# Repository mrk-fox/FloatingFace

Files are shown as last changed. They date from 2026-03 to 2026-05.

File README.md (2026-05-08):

<div align="center">
<h1>FloatingFace</h1><br>
  
A three-string-mounted small multifunctional cable roboter concept. <br>

 



<br>

Flowers
<div align="left">v1.0 aka "Floaty"</div>
</div>
<br>

FloatingFace is a roboter, mounted by 3mm paracord ropes at three points arranged in a triangle which achieves movement withing and under these 3 mounting points by tensioning or loosening each these ropes.

## Key features

- 3-points mount
- cheeseplate with additional servo for mechanization
- automatic calibration
- custom driver PCB with three TMC2209 slots
- redundant visual and magnetic travel distance encoder
- AS5600 magnetic encoders
- MPU5060
- possibility for rope pulley if higher loads applied

I built this project as proof-of-concept system for a 3-point-mounted, portable cable roboter with an universal extensions interface.

## PCB

Floaty has a custom-designed driver developer board for three TMC2209 drivers. Look at the design! <br>
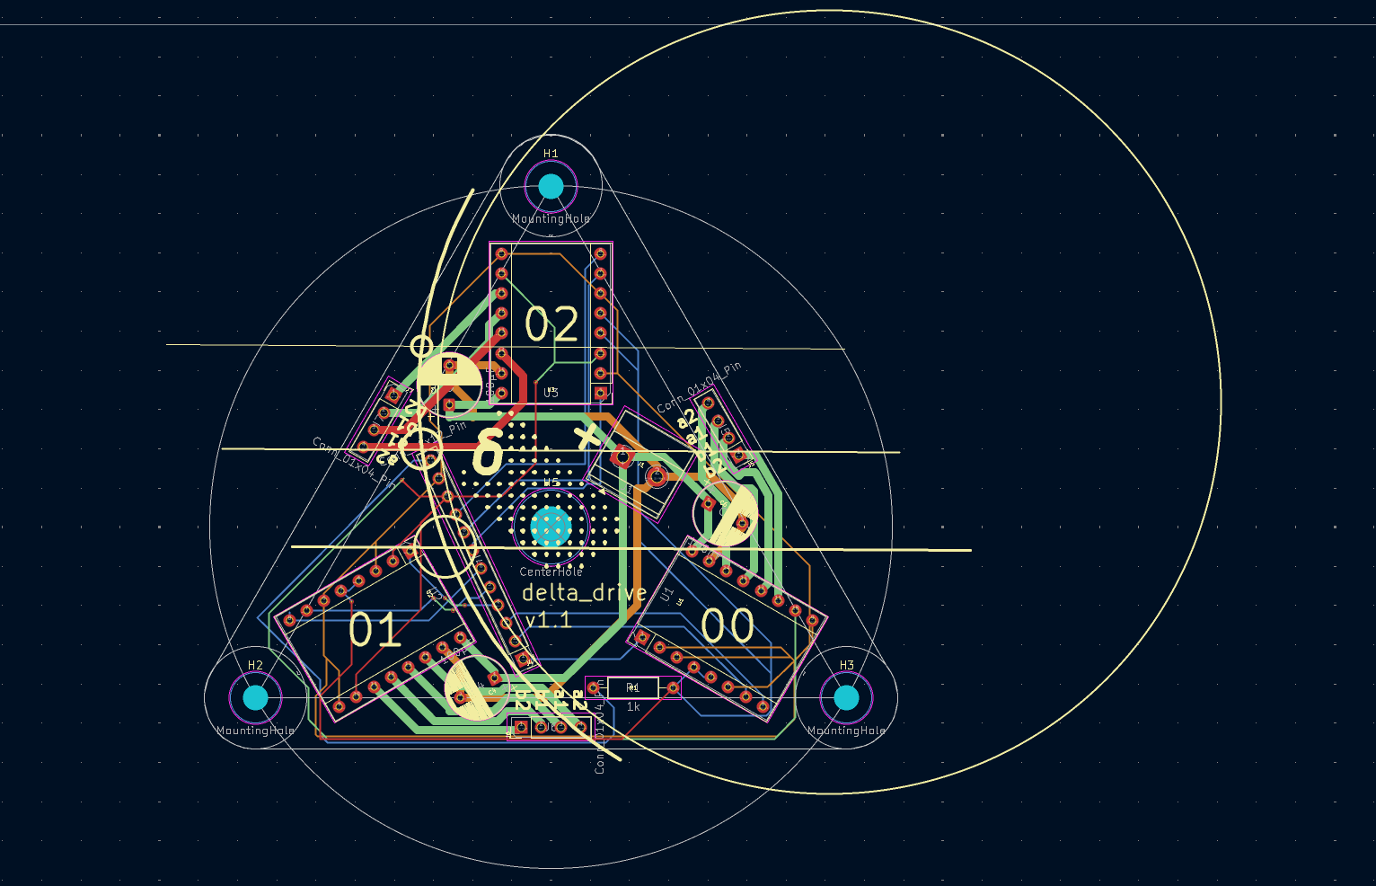
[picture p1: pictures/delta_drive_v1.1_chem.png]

Thats all the layers overlapped...
<br><br><br>
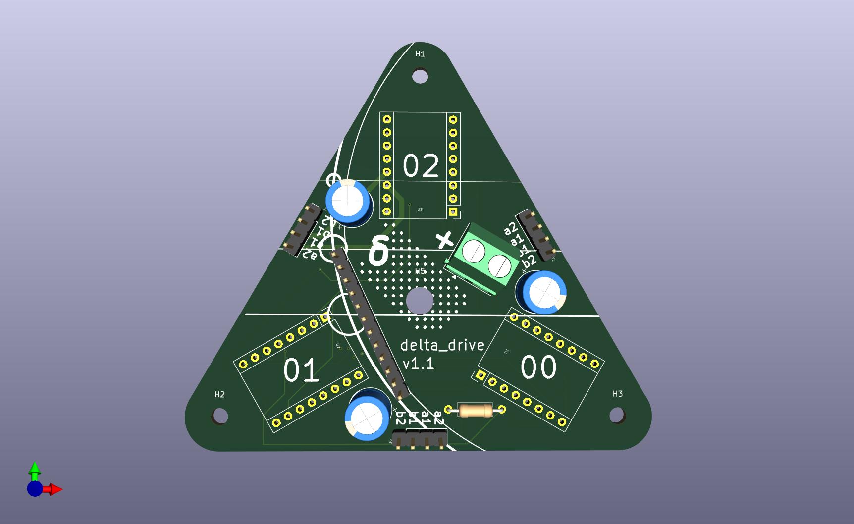
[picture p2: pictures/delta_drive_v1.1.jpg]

...and thats the front design. There is nothing on the back
<br><br><br>
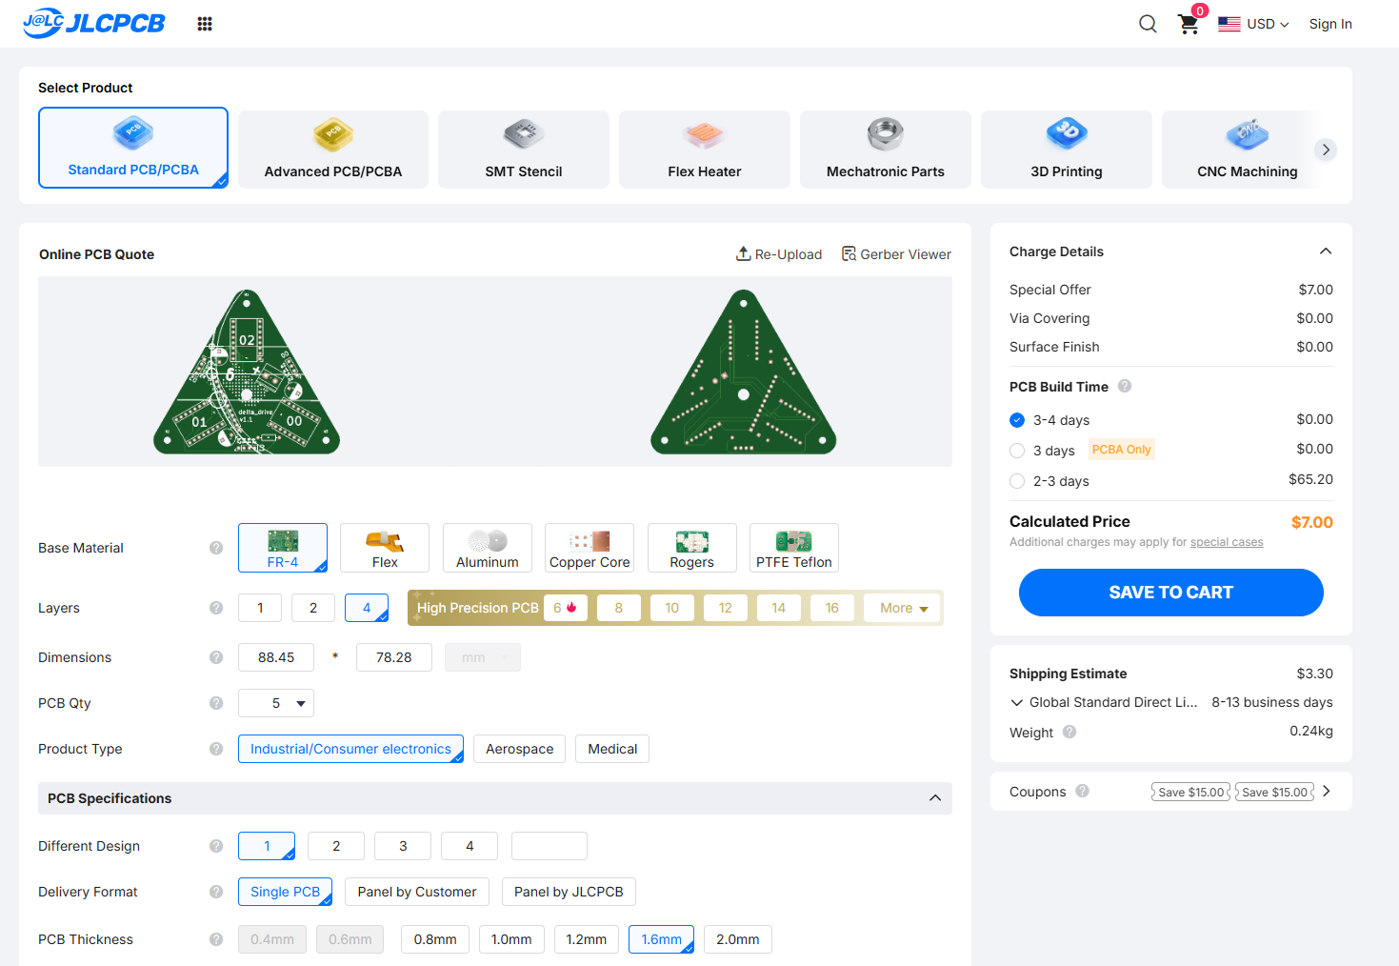
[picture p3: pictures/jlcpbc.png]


## Schematic
<br>
The overview schematic implementing a TCA9548 for the I2C controll of the three AS5600 sensors looks like this:
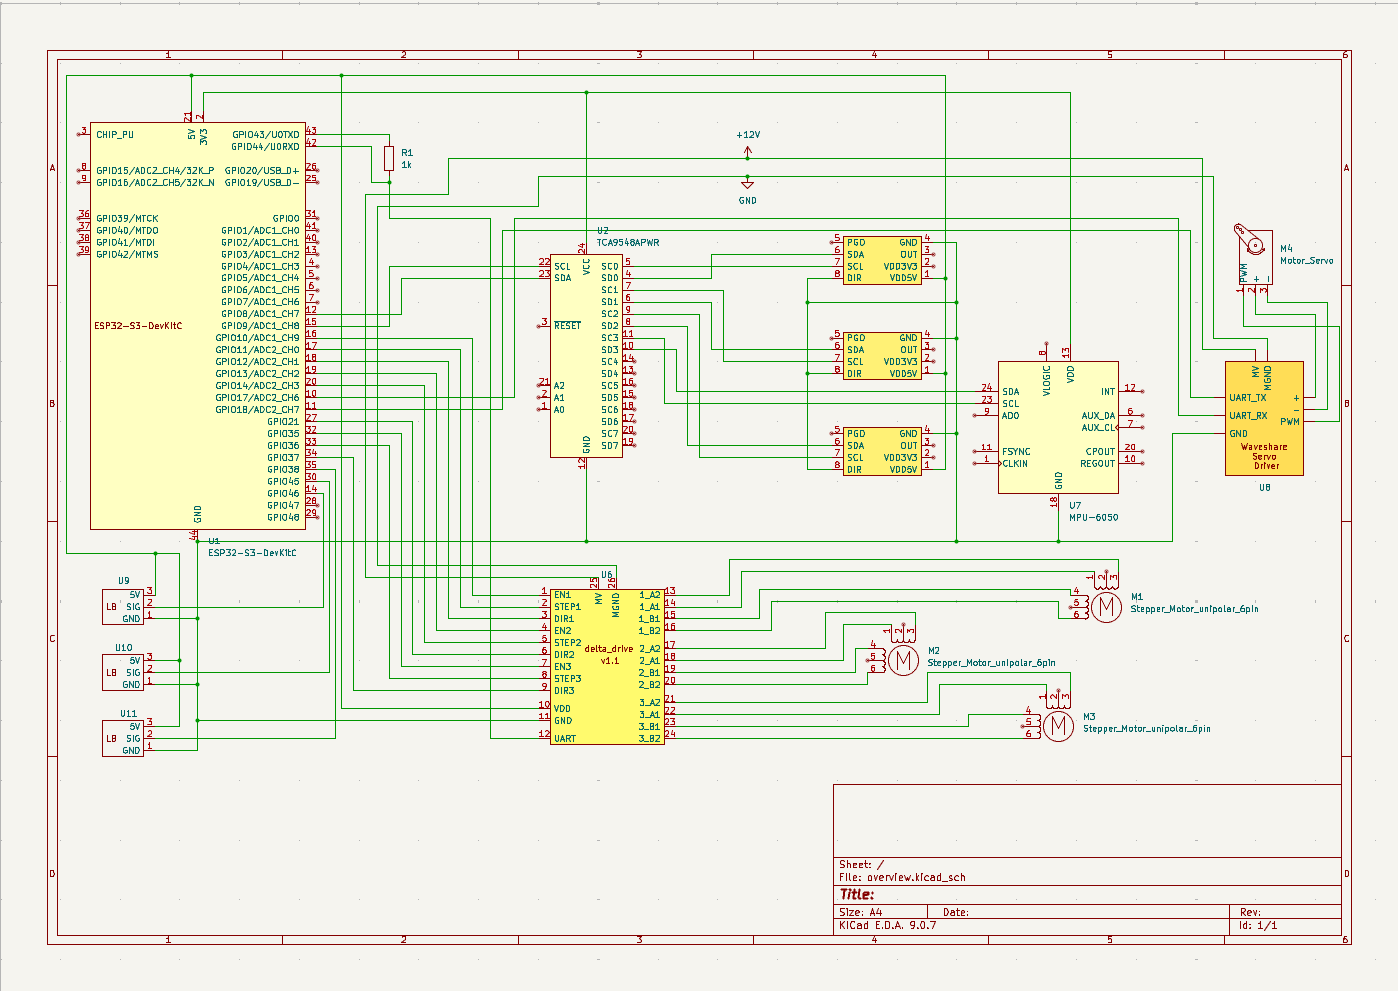
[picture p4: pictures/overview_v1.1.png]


and that is the schematic for the delta_drive v1.1:
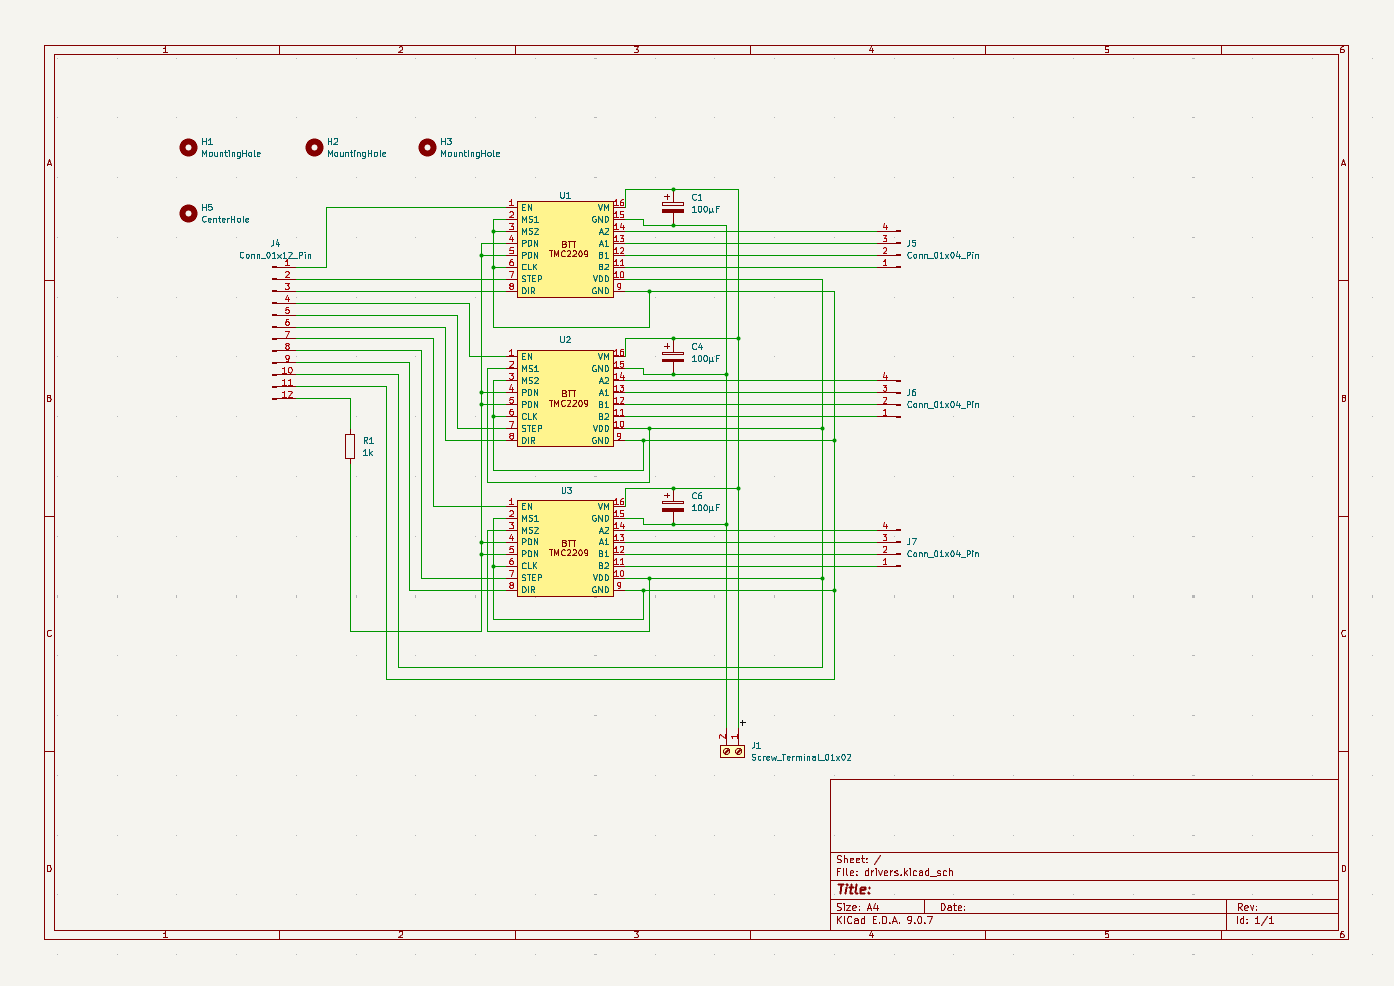
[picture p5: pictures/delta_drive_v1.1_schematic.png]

https://github.com/mrk-fox/FloatingFace/blob/main/pictures/delta_drive_v1.1_schematic.png

## Math
The basics were worked out with simple linear algebra, which are explained in this video together with the calibration process:

[The math behind "Floaty", the cable roboter](https://youtu.be/A8Sq22G1rsY)

Further, to make the implementation easier, all the calculation were modelled in Simulink:
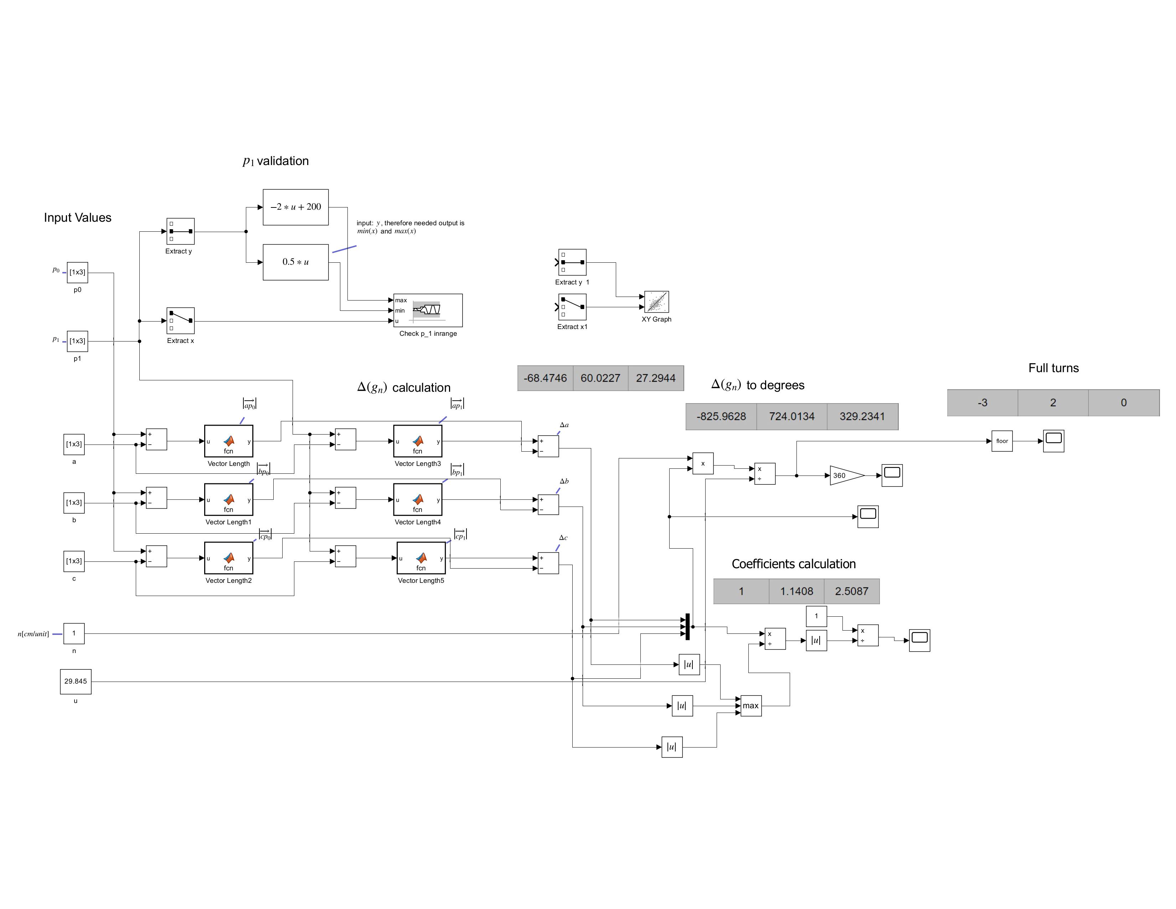
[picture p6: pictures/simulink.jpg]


<br>

The movement algorithm itself works on command through these steps:
1. Validate coordinates
2. Calculate $\Delta(g_n)$ (individual motor run vectors)
3. Calculate time-based movement coefficients $c(\Delta(g_n))$
4. Move in accordance to coefficitens slowly until all motor sensors register rising edge on light sensor
5. Re-calculate path
6. Move fast using PCNT counters
7. Slow down 2 guide sensor revolutions before movement finish
8. Proceed until finish on magnetic encoders feedback
9. Calibrate angles on finish

For angle calibration, Floaty uses the MP5060 sensor which gives an angle relative to gravity and the direction of the orthogonal of the angled face of the sensor. With that data an iterative funciton is started ajusting one motor step at a time until an angle less than 10 degrees is reached. 

## Assembly
The assembly is currently a prediciton of the possible steps. I doubt, that anyone will build this before me, but here we go:

1. Begin with the level one baseplate assemble the motors with the line drums and place them onto the baseplate
2. Mount the Servo and the MCU to the motor mount and baseplate
3. Assemble the 20x20 frame hexagon and mount the baseplate to the hexagon together with the line guides/sensing units
4. Assemble the secon level (electronics) and connect all electronics! (see below)
5. Fix everything together with the threaded rods and the spacers
6. Add the cheeseplate
7. Flash the firmware

## Cables

As the size of the robot is constrainted to certain limits, cable routing is crutial to ensure a safe and reliable operation. The following rules apply:
1. Zip-ties packaging the cable strands shoukd be placed every 2cm (0.787in)
2. Every cable leading to the line measurment units/motos should be placed in the through-leading holes of the appropriate third of the robot
3. A safe-zone of 1cm (0.393in) around the perimeter of the cutout of the basement plate for the line rolls should be cable-free to ensure a tangle-free operation
The mounting is done through running zip ties around the vertical spacers for the levels and the cable holes on the baseplates themselves.

## Zine Page

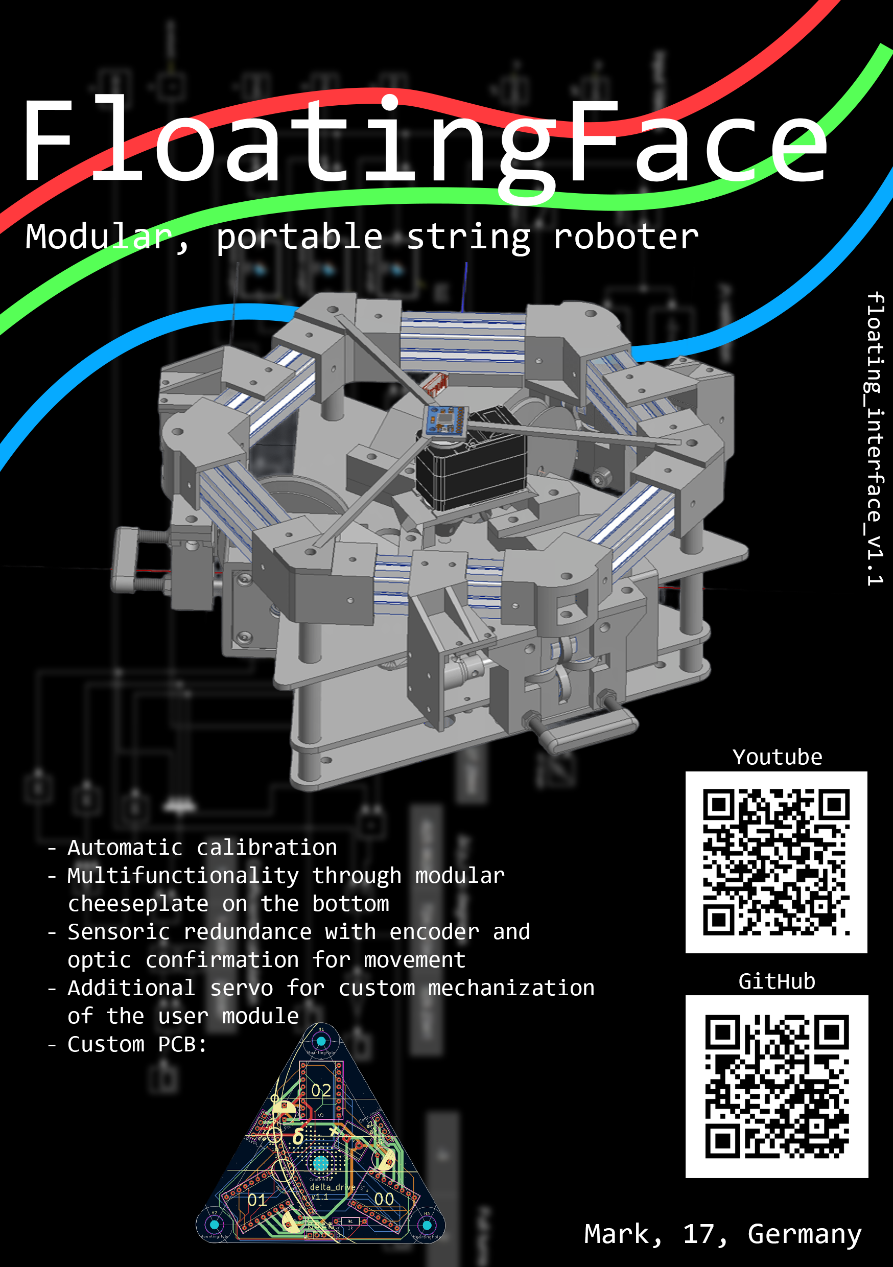
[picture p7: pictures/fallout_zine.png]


## Credit
I thank this project to... <br>
... [KiCad](https://www.kicad.org/)<br>
... [HackClub Fallout](https://fallout.hackclub.com/)<br>
... [Autodesk Inventor](https://www.autodesk.com/de/products/inventor/overview)<br>
... [BenjaminW](https://www.thingiverse.com/BenjaminW/designs) and [Serj Minin](https://grabcad.com/serj.minin-1) for the models

## License

This hardware project is licensed under the **CERN Open Hardware Licence v2 - Strongly Reciprocal (CERN-OHL-S)**.

See the [LICENSE](./LICENSE) file for details, or visit https://ohwr.org/cern_ohl_s_v2.

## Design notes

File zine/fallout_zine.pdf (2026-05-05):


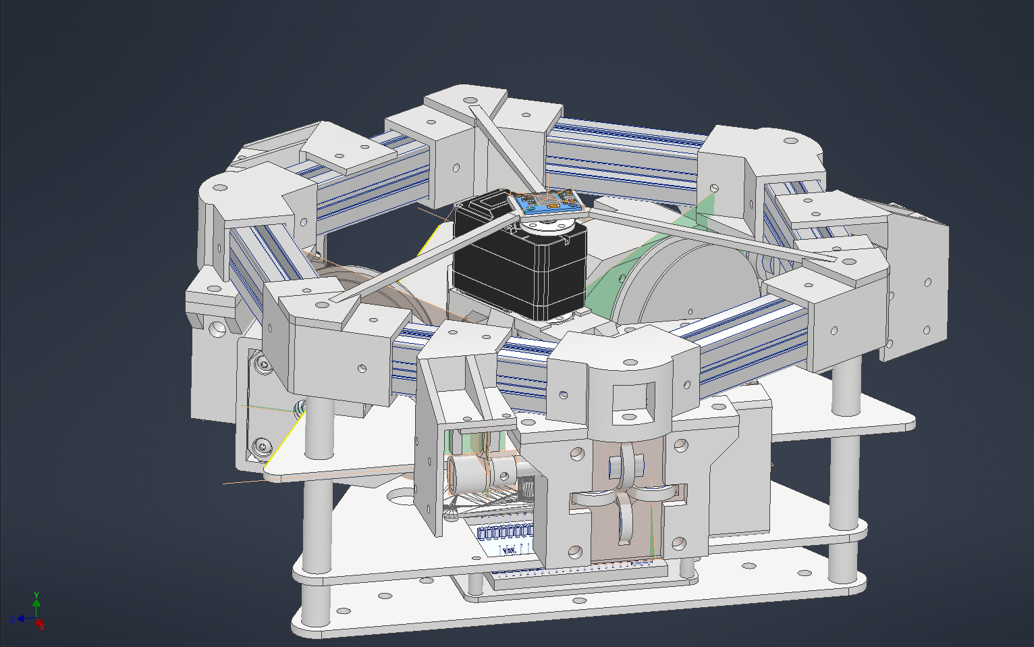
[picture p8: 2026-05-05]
pictures/full_design_v1.png

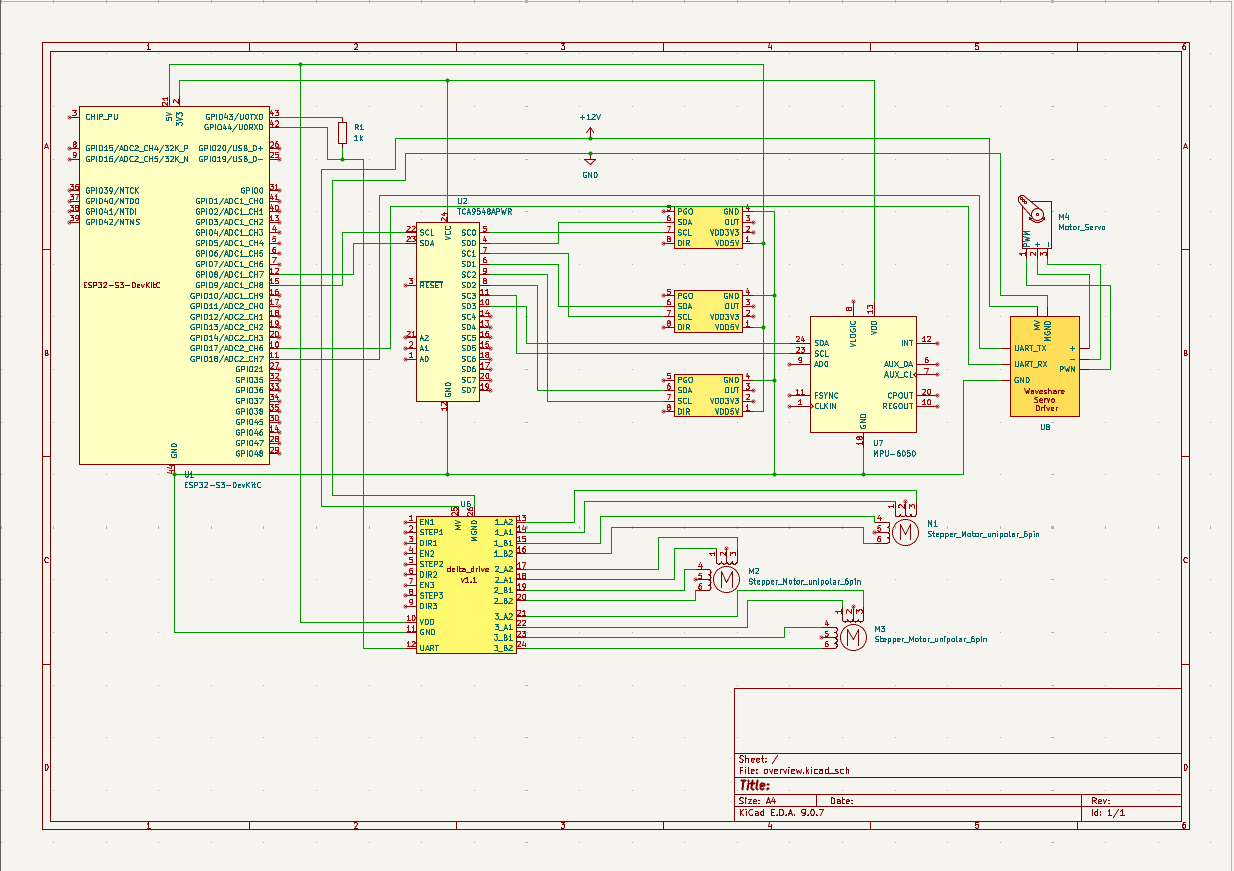
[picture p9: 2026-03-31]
pictures/overview_v1.png

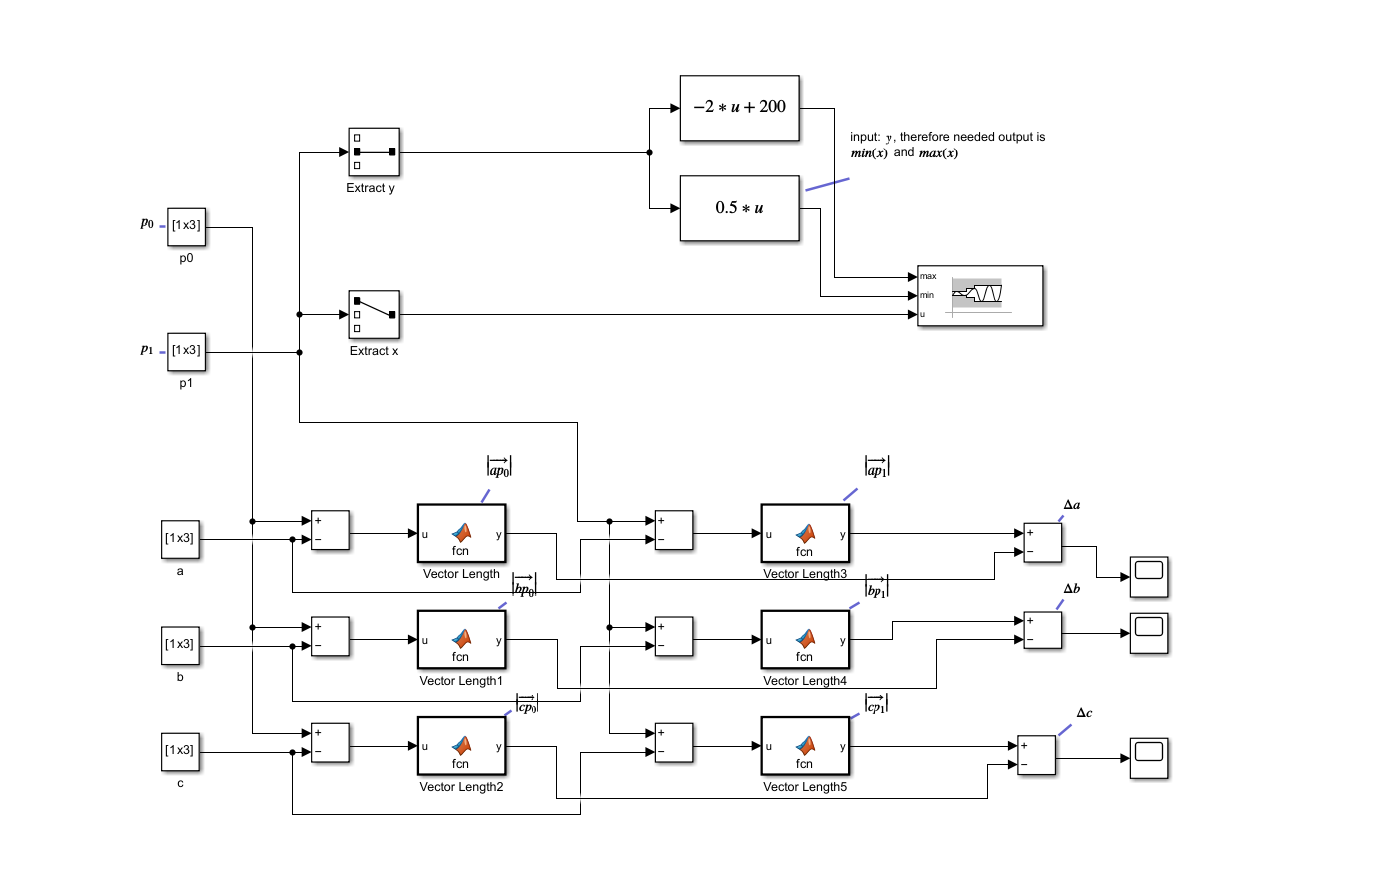
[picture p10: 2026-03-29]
pictures/simulink_first_design.png

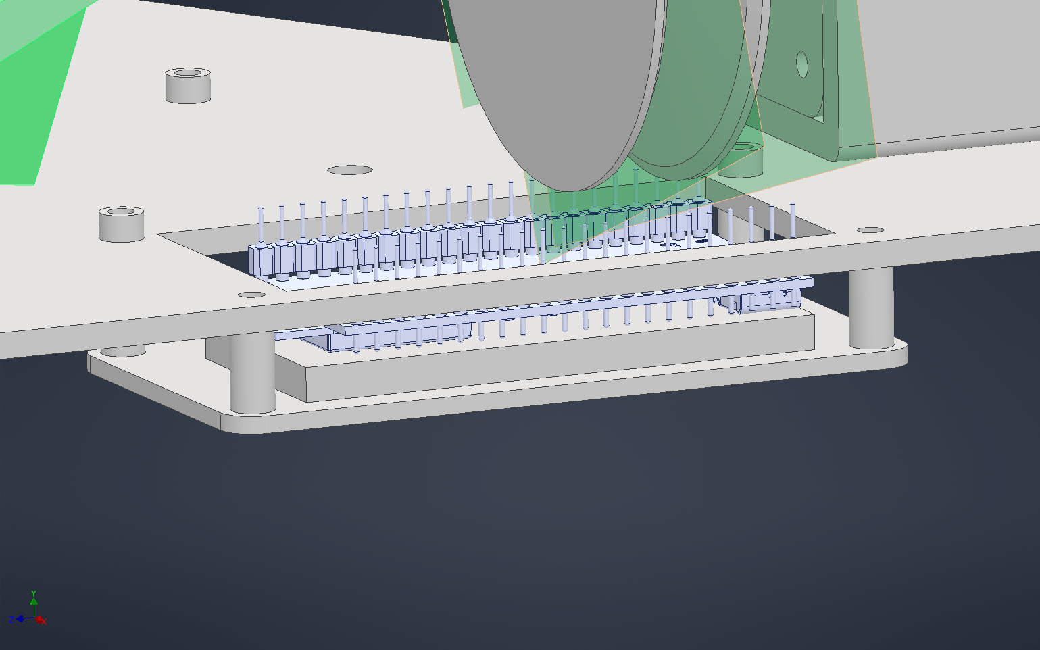
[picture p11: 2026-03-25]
pictures/esp_holder.png

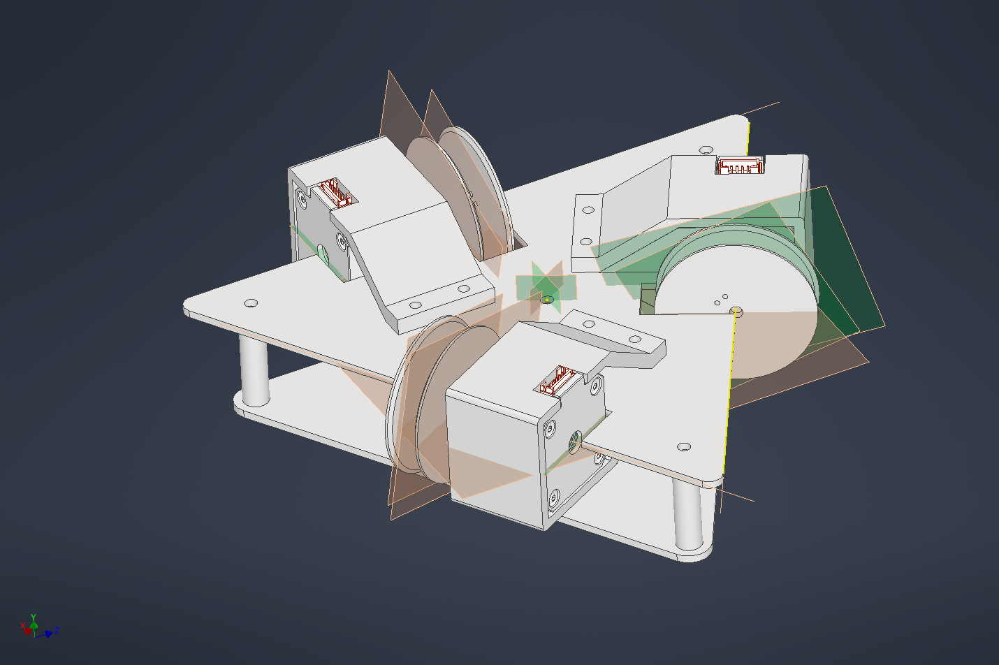
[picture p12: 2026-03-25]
pictures/stage_2_session_3.png

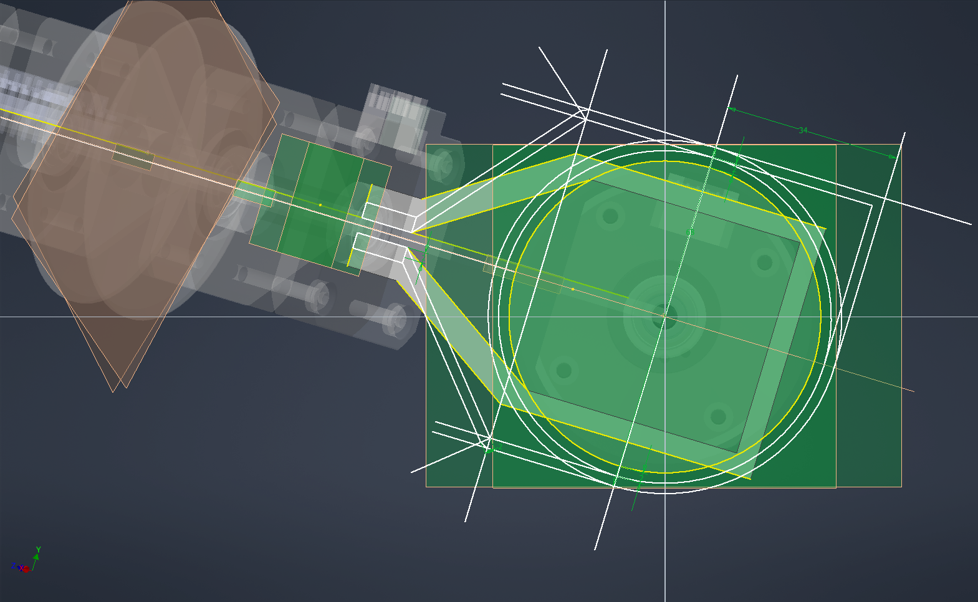
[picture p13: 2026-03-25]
pictures/drum_sketch.png

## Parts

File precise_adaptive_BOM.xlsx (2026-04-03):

Id | Part | Amount | Link | Price | Delivery | Note | Clearext link
1 | 695 Bearing | 15 | https://de.aliexpress.com/item/1005009937401862.html?curPageLogUid=iGQIs28VYHNF | $5.13 | $1.65 |  | link (https://de.aliexpress.com/item/1005009937401862.html?curPageLogUid=iGQIs28VYHNF)
2 | ST3215 Waveshare | 1 | https://www.waveshare.com/st3215-servo.htm?sku=22414 | $2.99 |  |  | https://www.waveshare.com/st3215-servo.htm?sku=22414
3 | Serial Bus Servo Driver Board | 1 | https://www.waveshare.com/product/modules/motors-servos/drivers/bus-servo-adapter-a.htm | $4.99 | $5.00 |  | https://www.waveshare.com/product/modules/motors-servos/drivers/bus-servo-adapter-a.htm
4 | TMC2209 Drivers | 4 | https://de.aliexpress.com/item/33028050145.html?curPageLogUid=4GoKWEk5BzJV | $10.52 |  | 4 is cheaper than 3 | link (https://de.aliexpress.com/item/33028050145.html?curPageLogUid=4GoKWEk5BzJV)
5 | 900mm 2020 Profile | 1 | https://www.ebay.de/itm/186710458751?chn=ps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 | 7.16 € |  |  | link (https://www.ebay.de/itm/186710458751?chn=ps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)
6 | U-Light Sensor | 3 | https://www.reichelt.de/de/de/shop/produkt/entwicklerboards_-_lichtschranken-zaehler-282555?PROVID=2788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 | 2.76 € | 5.59 € |  | link (https://www.reichelt.de/de/de/shop/produkt/entwicklerboards_-_lichtschranken-zaehler-282555?PROVID=2788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)
7 | 10x10x5 Neodym magnets | 5 | https://www.mtsmagnete.de/neodym-quader-magnete/quader-10mm-19mm/neodym-quadermagnet-10x10x5mm-neodym-beschichtung-grade-n45-magnetisiert-durch-5mm/a-2890/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 | 7.57 € | 0 € | Cheaper magnets have not the necessary documentation and polarity | link (https://www.mtsmagnete.de/neodym-quader-magnete/quader-10mm-19mm/neodym-quadermagnet-10x10x5mm-neodym-beschichtung-grade-n45-magnetisiert-durch-5mm/a-2890/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)
8 | AS5600 Magnetic Encodes | 3 | https://www.ebay.de/itm/264788915825?_skw=AS5600+Magnetic+Encodes&itmmeta=01KN7DF4Z81E5T057NKDKG36DB | 9.00 € | 1.56 € |  | link (https://www.ebay.de/itm/264788915825?_skw=AS5600+Magnetic+Encodes&itmmeta=01KN7DF4Z81E5T057NKDKG36DB)
9 | delta_drive v1.1 | 5 | https://jlcpcb.com/ | $7.00 | 3.30 € | smallest order qty | JLCPCB, see picture on github
10 | ESP32-S3-DevKitC-1 | 1 | https://de.aliexpress.com/item/1005009026897112.html?curPageLogUid=WkOrsh7gSksT | $7.77 |  |  | link (https://de.aliexpress.com/item/1005009026897112.html?curPageLogUid=WkOrsh7gSksT)
11 | TCA9548A | 1 | https://de.aliexpress.com/item/1005004996004241.html | $1.52 |  |  | link (https://de.aliexpress.com/item/1005004996004241.html)
12 | MPU 5060 | 1 | https://de.aliexpress.com/item/1005008796700745.html?curPageLogUid=eBqQMOrF5utz | $1.17 |  |  | link (https://de.aliexpress.com/item/1005008796700745.html?curPageLogUid=eBqQMOrF5utz)
13 | NEMA17 0.5Nm | 3 | https://de.aliexpress.com/item/1005011852081384.html?src=google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 | $12.27 |  |  | already got some
14 | 1kg ABS | 1 | https://eu.store.bambulab.com/de/products/abs-filament?id=46963746046300 | 25.99 € |  |  | https://eu.store.bambulab.com/de/products/abs-filament?id=46963746046300
 |  |  | all EUR entries | 52.48 € | 7.15 € | 59.63 €
 |  |  | all USD entries | $23.63 | $9.95 | $33.58
 |  |  |  | EUR/USD exchange: | 1.15
 |  |  |  | SUM:
 |  |  |  | $102.15
 |  |  |  |  |  |  | 3%

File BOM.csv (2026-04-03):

Part Name | Amount | Link | Price
695 Bearing | 15 | https://de.aliexpress.com/item/1005009937401862.html?curPageLogUid=iGQIs28VYHNF | $5,13
ST3215 Waveshare | 1 | https://www.waveshare.com/st3215-servo.htm?sku=22414 | $2,99
Serial Bus Servo Driver Board | 1 | https://www.waveshare.com/product/modules/motors-servos/drivers/bus-servo-adapter-a.htm | $4,99
TMC2209 Drivers | 4 | https://de.aliexpress.com/item/33028050145.html?curPageLogUid=4GoKWEk5BzJV | $10,52
900mm 2020 Profile | 1 | https://www.ebay.de/itm/186710458751?chn=ps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 | $8,25
U-Light Sensor | 3 | https://www.reichelt.de/de/de/shop/produkt/entwicklerboards_-_lichtschranken-zaehler-282555?PROVID=2788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 | $3,18
10x10x5 Neodym magnets | 5 | https://www.mtsmagnete.de/neodym-quader-magnete/quader-10mm-19mm/neodym-quadermagnet-10x10x5mm-neodym-beschichtung-grade-n45-magnetisiert-durch-5mm/a-2890/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 | $8,07
AS5600 Magnetic Encodes | 3 | https://www.ebay.de/itm/264788915825?_skw=AS5600+Magnetic+Encodes&itmmeta=01KN7DF4Z81E5T057NKDKG36DB | $10,35
delta_drive v1.1 | 5 | https://jlcpcb.com/ | $7,00
ESP32-S3-DevKitC-1 | 1 | https://de.aliexpress.com/item/1005009026897112.html?curPageLogUid=WkOrsh7gSksT | $7,77
TCA9548A | 1 | https://de.aliexpress.com/item/1005004996004241.html | $1,52
MPU 5060 | 1 | https://de.aliexpress.com/item/1005008796700745.html?curPageLogUid=eBqQMOrF5utz | $1,17
NEMA17 0.5Nm | 3 | https://de.aliexpress.com/item/1005011852081384.html?src=google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 | $12.27
1kg ABS | 1 | https://eu.store.bambulab.com/de/products/abs-filament?id=46963746046300 | $30,00

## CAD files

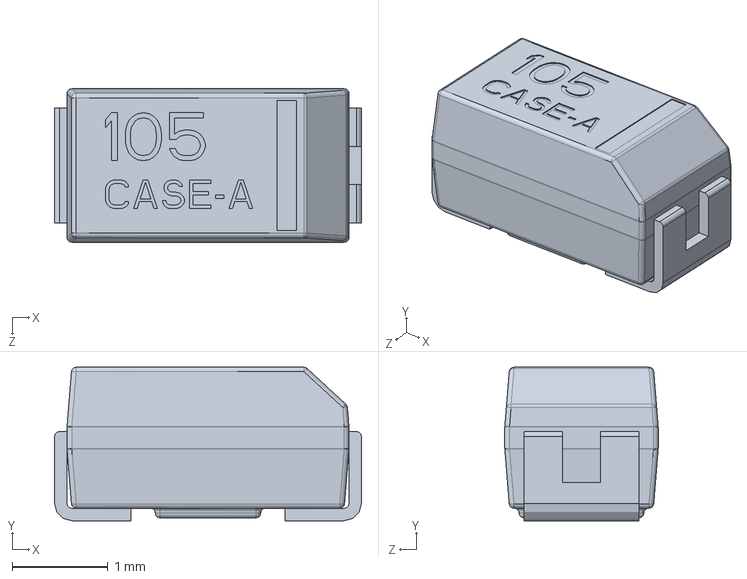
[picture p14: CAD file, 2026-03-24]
inventor_models/esp32-s3-wroom-1-1.snapshot.2/ctantal_case-a_l3-2_w1-6_h1-6.SLDPRT
3.20 x 1.60 x 1.60 mm

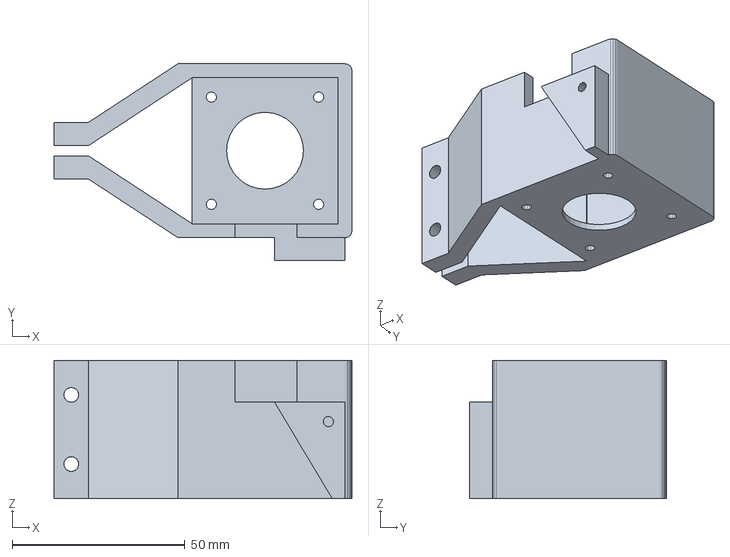
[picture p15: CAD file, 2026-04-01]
inventor_models/stl/nema_brackets_and_lineguides.3mf
86.1 x 56.8 x 40.0 mm

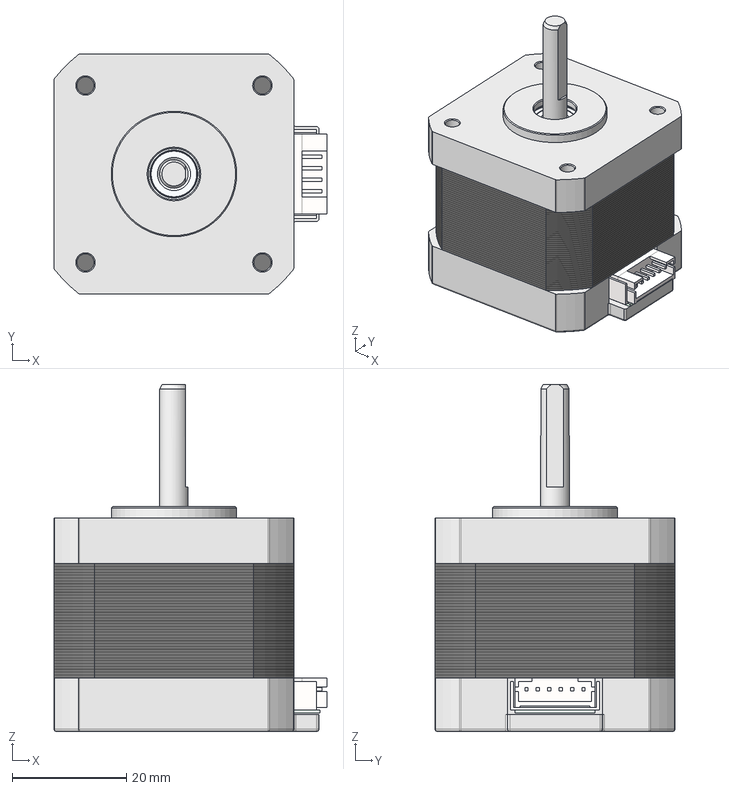
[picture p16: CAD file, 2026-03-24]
stl_models/17HS4401S_Stepper_Motor.step
47.8 x 42.0 x 60.8 mm
rear end cap
rear bearing
connector
shaft
stator
front end cap
front bearing
M3x10-Screw x 4

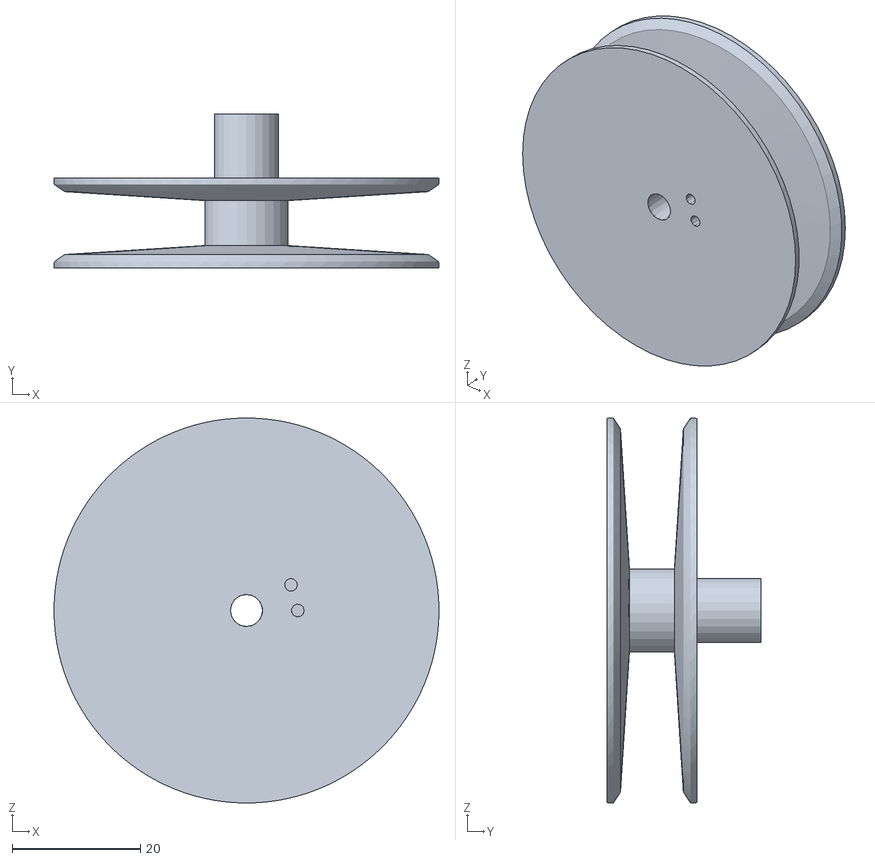
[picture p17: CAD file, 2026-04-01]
inventor_models/stl/spool.stl
60.0 x 24.0 x 60.0

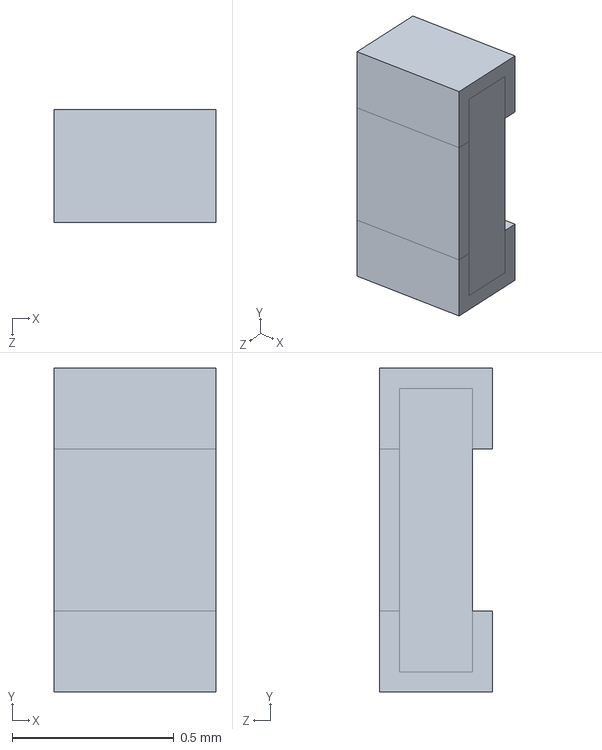
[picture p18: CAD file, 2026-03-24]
inventor_models/esp32-s3-wroom-1-1.snapshot.2/RC0402.SLDPRT
0.5 x 1.00 x 0.35 mm

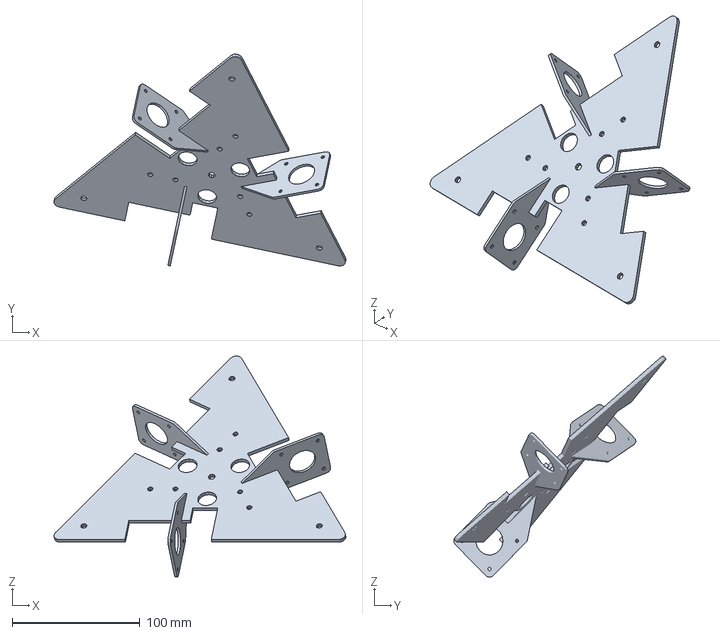
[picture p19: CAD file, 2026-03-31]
inventor_models/stl/baseplate.3mf
228.2 x 165.6 x 172.6 mm

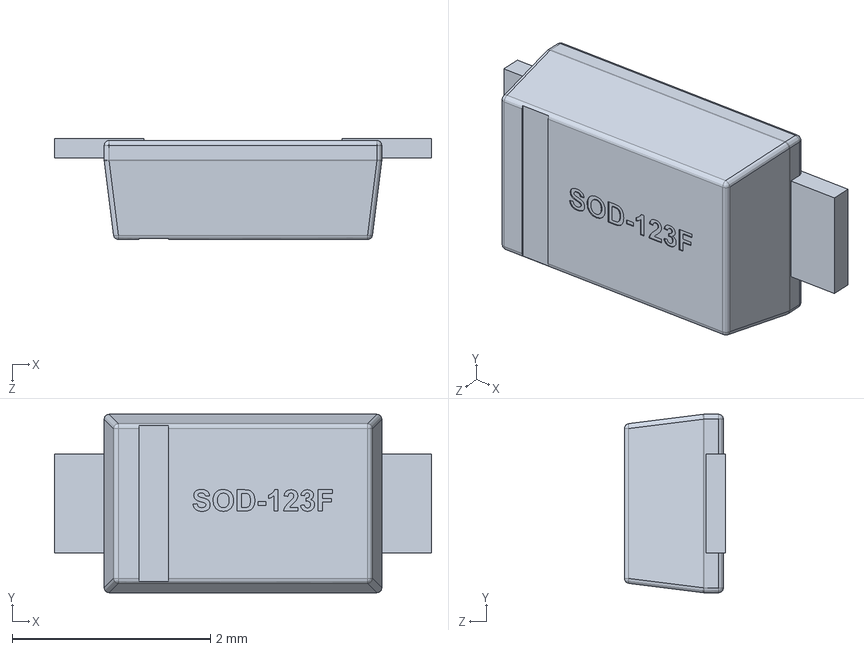
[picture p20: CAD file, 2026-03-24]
inventor_models/esp32-s3-wroom-1-1.snapshot.2/SOD-123F.SLDPRT
3.80 x 1.80 x 1.02 mm

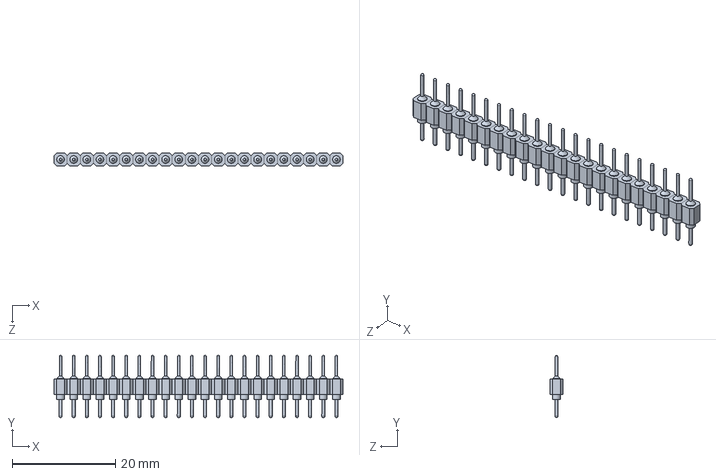
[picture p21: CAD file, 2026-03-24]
inventor_models/esp32-s3-wroom-1-1.snapshot.2/Штыревой разъем 22 конт шаг 2.54мм.SLDPRT
55.9 x 12.1 x 2.54 mm

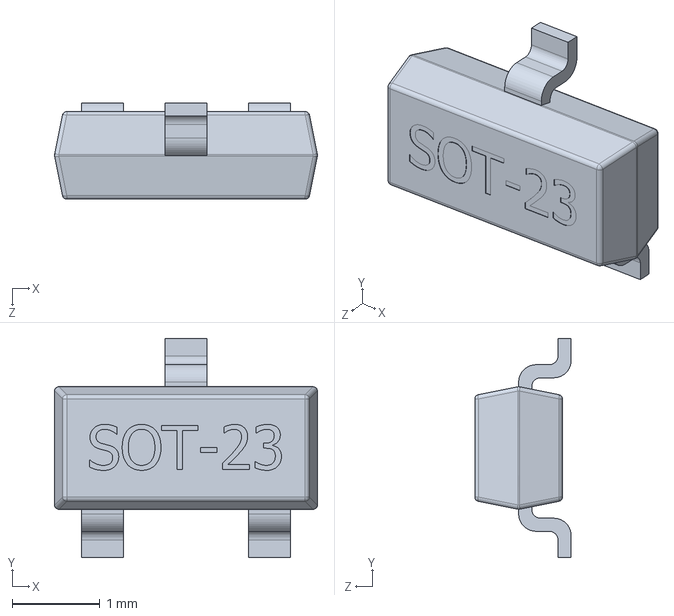
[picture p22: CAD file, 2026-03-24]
inventor_models/esp32-s3-wroom-1-1.snapshot.2/SOT23-3.SLDPRT
3.00 x 2.50 x 1.10 mm

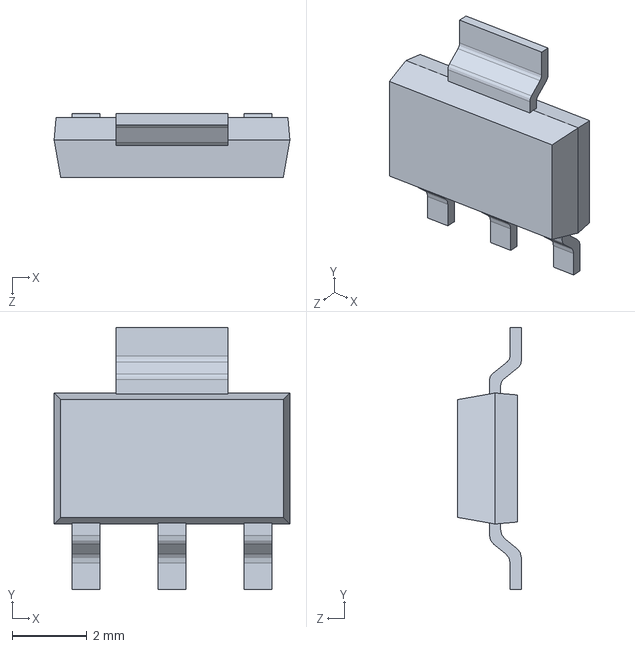
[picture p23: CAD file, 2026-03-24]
inventor_models/esp32-s3-wroom-1-1.snapshot.2/SOT-223.SLDPRT
6.30 x 7.00 x 1.70 mm

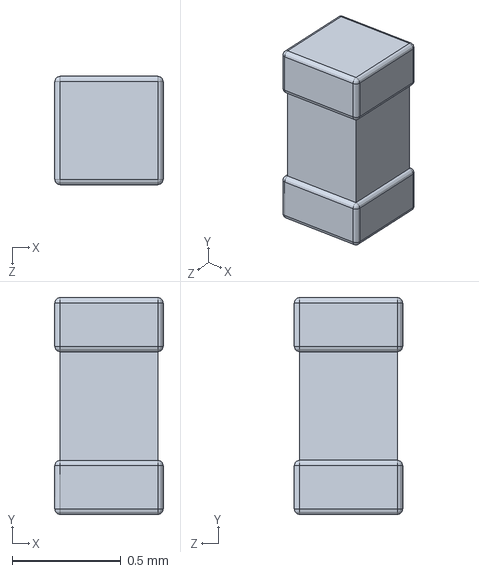
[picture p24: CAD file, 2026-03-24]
inventor_models/esp32-s3-wroom-1-1.snapshot.2/0402_CA_CB_CC_CD.SLDPRT
0.5 x 1.00 x 0.5 mm

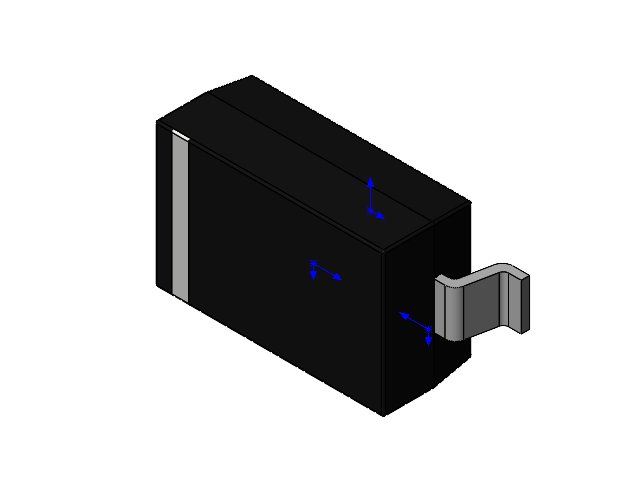
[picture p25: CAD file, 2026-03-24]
inventor_models/esp32-s3-wroom-1-1.snapshot.2/sod123 v4.SLDASM
pin.step
pin(Mirror).step
icbody_1.step
Component5.step

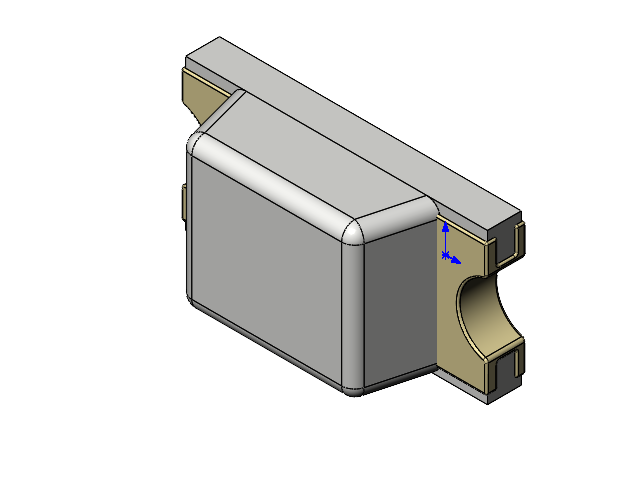
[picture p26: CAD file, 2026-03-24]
inventor_models/esp32-s3-wroom-1-1.snapshot.2/LED_0603 v4.SLDASM
Body.step
Cover.step
Cover_Mini.step
Insides.step

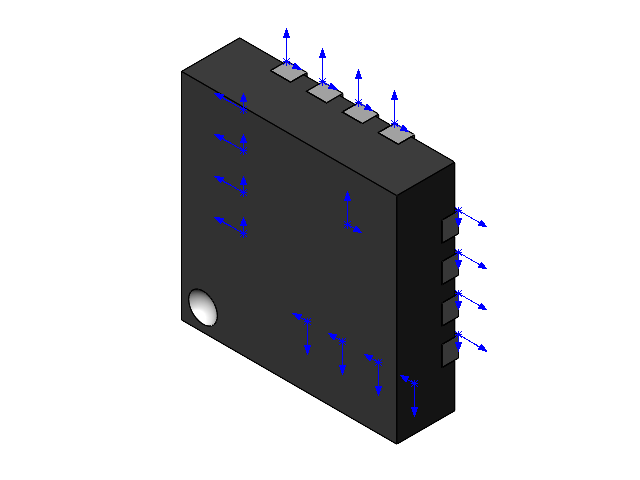
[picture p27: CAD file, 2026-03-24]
inventor_models/esp32-s3-wroom-1-1.snapshot.2/QFN-16 (3x3).SLDASM
QFN-16 (3x3) Part1.stp
QFN-16 (3x3) Part2.stp x 16
eBom-FreeParts.stp

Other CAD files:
inventor_models/esp32-s3-wroom-1-1.snapshot.2/Кнопка.SLDASM
inventor_models/esp32-s3-wroom-1-1.snapshot.2/USB-C.SLDASM
inventor_models/20-2020.dwg
inventor_models/17HS4401S_Stepper_Motor/17HS4401S_Stepper_Motor.iam
inventor_models/17HS4401S_Stepper_Motor/M3x10-Screw.ipt
inventor_models/17HS4401S_Stepper_Motor/OldVersions/17HS4401S_Stepper_Motor.0003.iam
inventor_models/17HS4401S_Stepper_Motor/connector.ipt
inventor_models/17HS4401S_Stepper_Motor/front bearing.ipt
inventor_models/17HS4401S_Stepper_Motor/front end cap.ipt
inventor_models/17HS4401S_Stepper_Motor/rear bearing.ipt
inventor_models/17HS4401S_Stepper_Motor/rear end cap.ipt
inventor_models/17HS4401S_Stepper_Motor/shaft.ipt
inventor_models/17HS4401S_Stepper_Motor/stator.ipt
inventor_models/2020_extrusion.ipt
inventor_models/2020_guide_adaptor.ipt
inventor_models/2020_nodes_conn.ipt
inventor_models/2020_top_guide_mnt.ipt
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

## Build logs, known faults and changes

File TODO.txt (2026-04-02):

TODO:
	- Make an admission TODO List based on Fallout

Mechanics:
	- Add screws/holding elements (1h)

Subtotal h=7

PCB/Electronics:
	- JLCPCB Order design: 2 (½h)

Programming/Math:
	- Calculate weight of construction (1½h) - 2,163kg +- 0.8%

Subtotal h=17

Documentation:
	- Add BOM (1h)
	- Convert to STL (1h)
	- Make good RM file on GH (2h)

Subtotal h=4

Total h=28, therefore ~4 intensive days

Documentation points that need to be  shown:
	- Describe the lvl feaures: Lvl1: Motors, Lvl2: conotroll: Lvl3: Interface
	- Custom bottom part -> Cheeseplate
	- Why did i choose the St3215 Servo? -> 12v, Modularity
	- 2020-to-vertecies t nut fixation
	- Why did i add the servo board spacers as a separate model?

ACTUALLY, ONLY 1 BIG TASKS LEFT!
- DOCU

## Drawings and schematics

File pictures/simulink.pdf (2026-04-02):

# validation

# Input Values

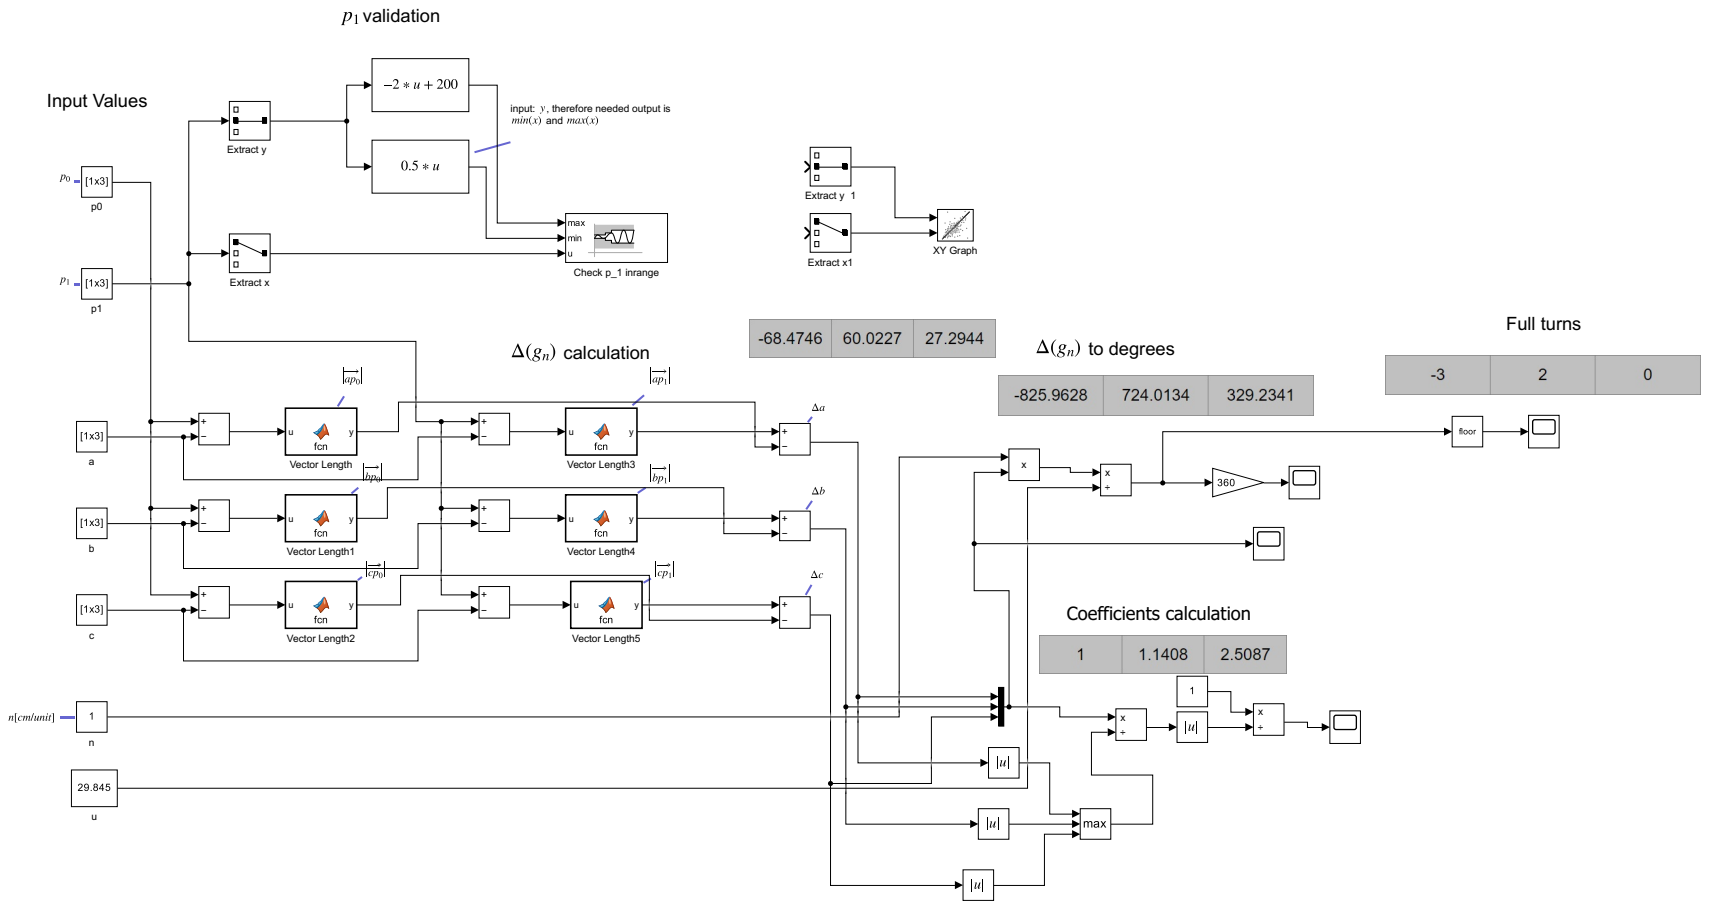
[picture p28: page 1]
calculation; and; Full turns; to degrees; Coefficients calculation; Extract x; Extract y; Check p_1 inrange; Vector Length; XY Graph; Extract y 1; Extract x1; Vector Length1; Vector Length2; Vector Length3; Vector Length4; Vector Length5

input: , therefore needed output is

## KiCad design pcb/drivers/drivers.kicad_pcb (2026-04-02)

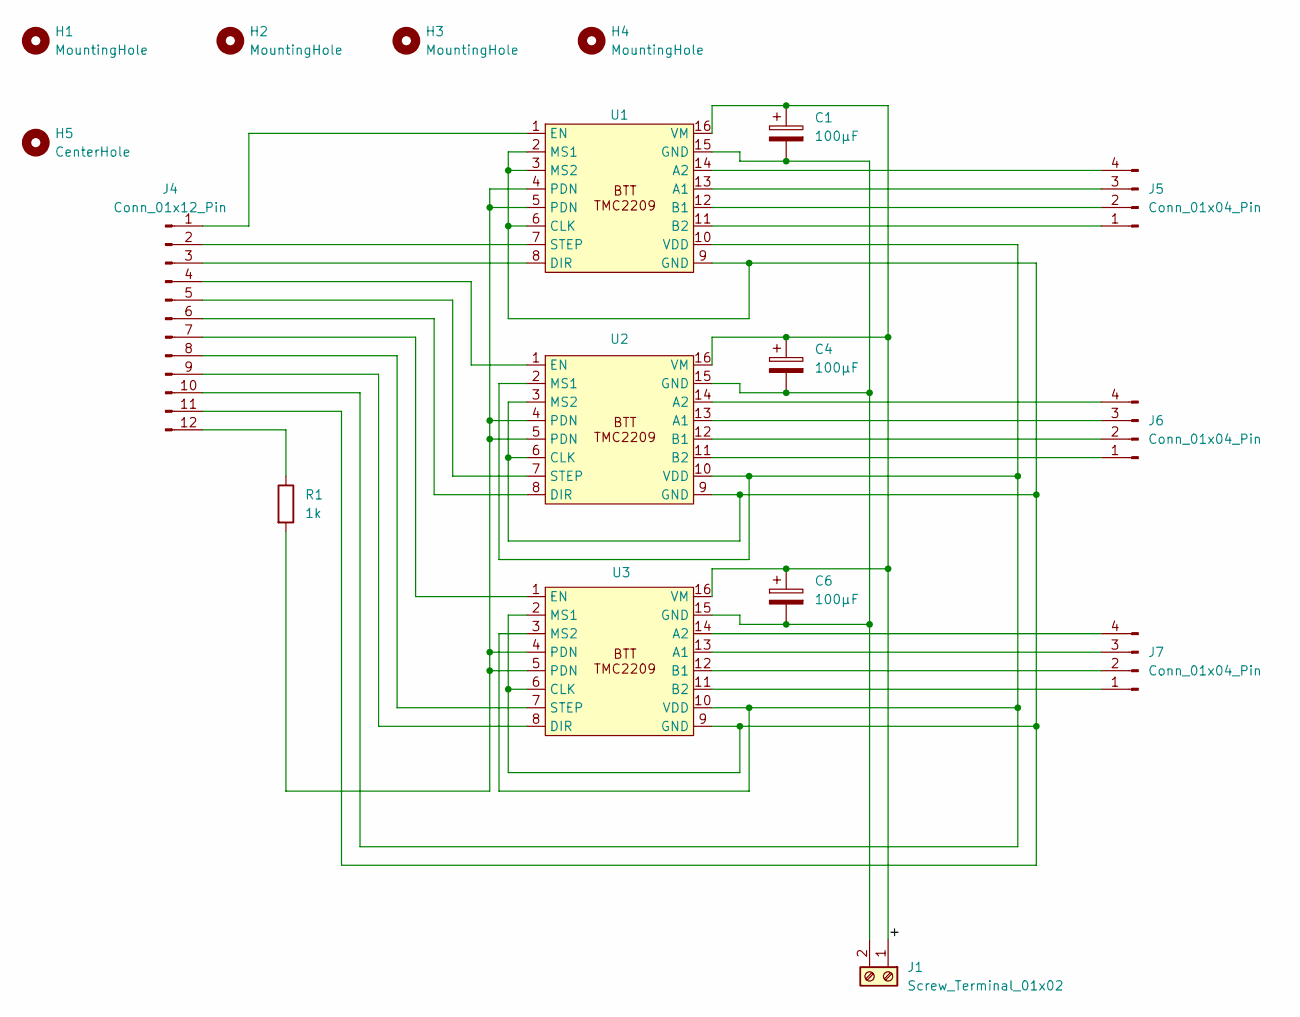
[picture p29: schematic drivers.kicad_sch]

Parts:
C1, C4, C6: 100µF; CP_Radial_D8.0mm_P5.00mm
H1, H2, H3, H4: MountingHole; MountingHole_3.2mm_M3
H5: CenterHole; MountingHole_5.3mm_M5_ISO7380
J1: Screw_Terminal_01x02; TerminalBlock_Phoenix_MKDS-1,5-2-5.08_1x02_P5.08mm_Horizont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
J4: Conn_01x12_Pin; PinHeader_1x12_P2.54mm_Vertical
J5, J6, J7: Conn_01x04_Pin; PinHeader_1x04_P2.54mm_Vertical
R1: 1k; R_Axial_DIN0207_L6.3mm_D2.5mm_P10.16mm_Horizontal
U1, U2, U3: TMC2209-Breakout

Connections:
/+: C1.1, C4.1, C6.1, J1.1, U1.16 (VM), U2.16 (VM), U3.16 (VM)
unnamed: C1.2, C4.2, C6.2, J1.2, U1.15 (GND), U2.15 (GND), U3.15 (GND)
unnamed: J4.1, U1.1 (EN)
unnamed: J4.2, U1.7 (STEP)
unnamed: J4.3, U1.8 (DIR)
unnamed: J4.4, U2.1 (EN)
unnamed: J4.5, U2.7 (STEP)
unnamed: J4.6, U2.8 (DIR)
unnamed: J4.7, U3.1 (EN)
unnamed: J4.8, U3.7 (STEP)
unnamed: J4.9, U3.8 (DIR)
unnamed: J4.10, U1.10 (VDD), U2.2 (MS1), U2.10 (VDD), U3.3 (MS2), U3.10 (VDD)
unnamed: J4.11, U1.2 (MS1), U1.3 (MS2), U1.6 (CLK), U1.9 (GND), U2.3 (MS2), U2.6 (CLK), U2.9 (GND), U3.2 (MS1), U3.6 (CLK), U3.9 (GND)
unnamed: J4.12, R1.1
unnamed: J5.1, U1.11 (B2)
unnamed: J5.2, U1.12 (B1)
unnamed: J5.3, U1.13 (A1)
unnamed: J5.4, U1.14 (A2)
unnamed: J6.1, U2.11 (B2)
unnamed: J6.2, U2.12 (B1)
unnamed: J6.3, U2.13 (A1)
unnamed: J6.4, U2.14 (A2)
unnamed: J7.1, U3.11 (B2)
unnamed: J7.2, U3.12 (B1)
unnamed: J7.3, U3.13 (A1)
unnamed: J7.4, U3.14 (A2)
unnamed: R1.2, U1.4 (PDN), U1.5 (PDN), U2.4 (PDN), U2.5 (PDN), U3.4 (PDN), U3.5 (PDN)

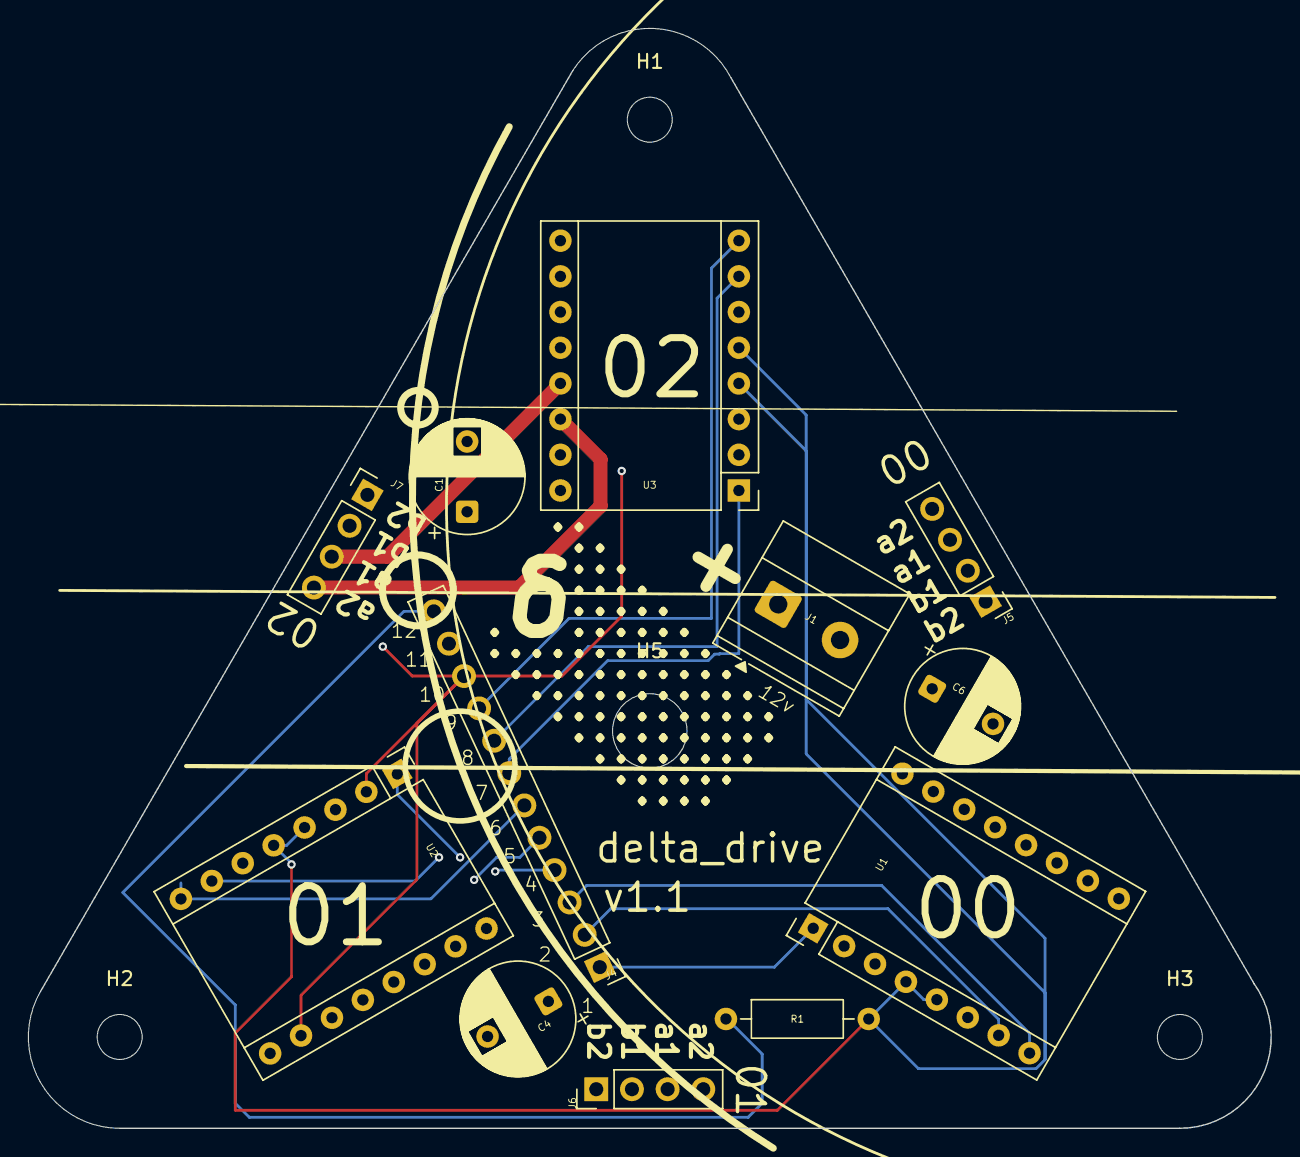
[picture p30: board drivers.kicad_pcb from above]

Board: 4 copper layers, 88.4 x 78.3 mm, 17 parts (0 on the bottom side), 27 nets.

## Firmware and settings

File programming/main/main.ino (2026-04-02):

//Copyright 2026 Mark Scharonow

//This source describes Open Hardware and is licensed under the CERN-OHL-S v2.

//You may redistribute and modify this source and make products using it
//under the terms of the CERN-OHL-S v2 (https://ohwr.org/cern_ohl_s_v2).

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
//Source location: https://github.com/mrk-fox/FloatingFace

//goal:init all TMCs and start reading torque

//0->a 1->b 2->c
#include "driver/pulse_cnt.h"
#include <TMCStepper.h>
#include "I2Cdev.h"
#include "MPU6050.h"
#include <AS5600.h>
#include <Wire.h>
#include <math.h>

#define I2C_SDA 12
#define I2C_SCL 15
#define EN_0 16
#define STEP_0 17
#define DIR_0 18
#define EN_1 19
#define STEP_1 20
#define DIR_1 27
#define EN_2 32
#define STEP_2 33
#define DIR_2 34

#define UART_TMC_RX 42
#define UART_TMC_TX 43

#define LB_0 35
#define LB_1 30
#define LB_2 14


#define PULSE_GPIO_0  35
#define PULSE_GPIO_1  30
#define PULSE_GPIO_2  14

#define DRIVER_ADDR_0 0b00
#define DRIVER_ADDR_1 0b01
#define DRIVER_ADDR_2 0b10
#define TCA_ADDR 0x70

#define SERIAL_PORT Serial0

#define R_SENSE 0.11f

#define U 29.845

bool valid_tilt;

//-------------------Motors-----------------------------

using namespace TMC2208_n;

TMC2209Stepper driver0(&SERIAL_PORT, R_SENSE, DRIVER_ADDR_0);
TMC2209Stepper driver1(&SERIAL_PORT, R_SENSE, DRIVER_ADDR_1);
TMC2209Stepper driver2(&SERIAL_PORT, R_SENSE, DRIVER_ADDR_2);

TMC2209Stepper* drivers[] = { &driver0, &driver1, &driver2 };
const uint8_t NUM_DRV = 3;

//---------------------Angles----------------------------

// Forward declaration so AngleTracker can call tca_select before it's defined
void tca_select(uint8_t channel);

class AngleTracker {
  AS5600* _sensor;
  uint8_t _channel;
  float _startAngle;
  bool _active = false;

  float readDeg() {
    tca_select(_channel);
    return _sensor->readAngle() * AS5600_RAW_TO_DEGREES;
  }

public:
  AngleTracker(AS5600* sensor, uint8_t channel)
    : _sensor(sensor), _channel(channel) {}

  void begin() {
    tca_select(_channel);
    _sensor->begin();
    if (!_sensor->isConnected()) {
      Serial.print("ERR: Sensor on channel ");
      Serial.print(_channel);
      Serial.println(" not found");
    }
  }

  void start() {
    _startAngle = readDeg();
    _active = true;
  }

  void stop() {
    _active = false;
  }

  float delta() {
    if (!_active) return 0;
    float d = readDeg() - _startAngle;
    if (d > 180)  d -= 360;
    if (d < -180) d += 360;
    return d;
  }

  bool isActive() { return _active; }
};

//tracker0.begin() -> init sensor
//tracker0.start() -> set zero, begin measurement
//tracker0.stop()  -> end measurement
//tracker0.delta() -> angle change since start() in degrees
//tracker0.isActive() -> is the measurement active?

AS5600 sensor0;
AS5600 sensor1;
AS5600 sensor2;

AngleTracker tracker0(&sensor0, 0);
AngleTracker tracker1(&sensor1, 1);
AngleTracker tracker2(&sensor2, 2);

// Fixed: int[] is invalid in C++; use int name[size]
int p0[3] = {0, 0, 0};
int p1[3] = {0, 0, 0};
int a[3]  = {0, 0, 0}; // set anchor values here
int b[3]  = {50, 100, 0};
int c[3]  = {100, 0, 0};
float n = 0; // set cm/unit value here

void tca_select(uint8_t channel) {
  if (channel > 7) return;
  Wire.beginTransmission(TCA_ADDR);
  Wire.write(1 << channel);
  Wire.endTransmission();
}

pcnt_unit_handle_t units[3];
int gpios[] = {PULSE_GPIO_0, PULSE_GPIO_1, PULSE_GPIO_2};

//------------------------TILT_ANGLES----------------------

MPU6050 mpu;

struct TiltResult {
  float tiltAngle;     // 0° = flat, 90° = vertical
  float tiltDirection; // -180° to +180° relative to sensor X-axis
  bool  valid;         // false if sensor read failed (e.g. free-fall)
};

TiltResult getTilt() {
  int16_t ax, ay, az, gx, gy, gz;
  mpu.getMotion6(&ax, &ay, &az, &gx, &gy, &gz);

  float ax_f = ax / 16384.0f;
  float ay_f = ay / 16384.0f;
  float az_f = az / 16384.0f;

  float mag = sqrt(ax_f*ax_f + ay_f*ay_f + az_f*az_f);
  if (mag < 0.001f) return {0, 0, false}; // free-fall / bad read

  ax_f /= mag;
  ay_f /= mag;
  az_f /= mag;

  return {
    acos(constrain(az_f, -1.0f, 1.0f)) * 180.0f / PI,
    atan2(ay_f, ax_f) * 180.0f / PI,
    true
  };
}



//--------------------------SETUP--------------------------

void setup() {
  Wire.begin(I2C_SDA, I2C_SCL);
  Serial.begin(115200);
  while (!Serial);
  Serial.println("\nStart...");

  SERIAL_PORT.begin(115200);
  mpu.initialize();

  if (!mpu.testConnection()) {
    Serial.println("MPU6050 connection failed!");
    while (true);
  }

  for (int i = 0; i < NUM_DRV; i++) {
    drivers[i]->beginSerial(115200);
    drivers[i]->begin();
    drivers[i]->toff(4);
    drivers[i]->TCOOLTHRS(0xFFFFFF); // Fixed: missing semicolon
    drivers[i]->SGTHRS(40);
    drivers[i]->en_spreadCycle(false);
    drivers[i]->pdn_disable(true);
  }

  pinMode(EN_0,   OUTPUT);
  pinMode(EN_1,   OUTPUT);
  pinMode(EN_2,   OUTPUT);
  pinMode(DIR_0,  OUTPUT);
  pinMode(DIR_1,  OUTPUT);
  pinMode(DIR_2,  OUTPUT);
  pinMode(STEP_0, OUTPUT);
  pinMode(STEP_1, OUTPUT);
  pinMode(STEP_2, OUTPUT);

  pinMode(LB_0, INPUT);
  pinMode(LB_1, INPUT);
  pinMode(LB_2, INPUT);

  digitalWrite(EN_0,  LOW);
  digitalWrite(EN_1,  LOW);
  digitalWrite(EN_2,  LOW);
  digitalWrite(DIR_0, HIGH); // direction TBD in testing
  digitalWrite(DIR_1, HIGH);
  digitalWrite(DIR_2, HIGH);

  // Fixed: replaced manual sensor init + undeclared offset0/1/2
  //        with the AngleTracker system that already handles this
  tracker0.begin();
  tracker1.begin();
  tracker2.begin();

  pcnt_unit_config_t unit_config = {
    .low_limit  = -32768,
    .high_limit =  32767,
  };

  for (int i = 0; i < 3; i++) {
      pcntInitRising(gpios[i], &units[i]);
  }
  
  tension();
  tdc();
}


//pcnt_unit_get_count(units[i], &counts[i]);  /get prct and store it in counts[i]
//pcnt_unit_clear_count(units[i]); //set prct unit i to 0

//-------------------------LOOP----------------------------------

void loop() {
  for (int i = 0; i < NUM_DRV; i++) { // Fixed: was "int = 0"
    uint16_t sg = drivers[i]->sg_result();
    Serial.print("Motor ");
    Serial.print(i);
    Serial.print(" SG: "); // Fixed: missing semicolon
    Serial.println(sg);
  }
  delay(100); // Fixed: missing semicolon
}

//-----------------METHODS-------------------------

// Forward declaration so tension/blind_x can call get_torque_n before it's defined
uint16_t get_torque_n(int num);

bool tension() {
  for (int i = 500; i > 150; i -= 50) { // Fixed: was "int = 500"
    while (get_torque_n(0) >= i || get_torque_n(1) >= i || get_torque_n(2) >= i) {
      digitalWrite(STEP_0, HIGH);
      digitalWrite(STEP_1, HIGH);
      digitalWrite(STEP_2, HIGH);
      delay(200);
      digitalWrite(STEP_0, LOW);
      digitalWrite(STEP_1, LOW);
      digitalWrite(STEP_2, LOW);
      delay(200);
    }
  }
  return true;
}

void read_tilt_angles() {
  TiltResult t = getTilt();
  if (t.valid) { valid_tilt = true;} else {
    Serial.println("Invalid reading (free-fall or sensor error)");
  }
}

float get_tilt_angle() { TiltResult t = getTilt(); return t.tiltAngle; }
float get_tilt_dir()   { TiltResult t = getTilt(); return t.tiltDirection; }

int get_max_v_pos(float* delta_g, float match) {
  if (delta_g[0] == match) {
    return 0;
  } else if (delta_g[1] == match) {
    return 1;
  } else {
    return 2;
  }
}


//--------------------CALIBRATION--------------------

bool tdc() {
  calibrate_distance_ab();
  calibrate_distance_bc();
  calibrate_distance_ca();
  return true;
}

bool blind_a() {
  digitalWrite(DIR_0, HIGH);
  digitalWrite(DIR_1, LOW);
  digitalWrite(DIR_2, LOW);
  while (get_torque_n(0) != 0) { // TODO: replace with threshold, != 0 is fragile on noisy SG
    if (get_torque_n(1) < 100) {
      digitalWrite(STEP_1, HIGH);
      digitalWrite(STEP_1, LOW);
    }
    if (get_torque_n(2) < 100) {
      digitalWrite(STEP_2, HIGH);
      digitalWrite(STEP_2, LOW);
    }
    digitalWrite(STEP_0, HIGH);
    delay(200);
    digitalWrite(STEP_0, LOW);
    delay(200);
  }
  return true;
}

bool blind_b() {
  digitalWrite(DIR_0, LOW);
  digitalWrite(DIR_1, HIGH);
  digitalWrite(DIR_2, LOW);
  while (get_torque_n(1) != 0) {
    if (get_torque_n(0) < 100) {
      digitalWrite(STEP_0, HIGH);
      digitalWrite(STEP_0, LOW);
    }
    if (get_torque_n(2) < 100) {
      digitalWrite(STEP_2, HIGH);
      digitalWrite(STEP_2, LOW);
    }
    digitalWrite(STEP_1, HIGH);
    delay(200);
    digitalWrite(STEP_1, LOW);
    delay(200);
  }
  return true;
}

bool blind_c() {
  digitalWrite(DIR_0, LOW);
  digitalWrite(DIR_1, LOW);
  digitalWrite(DIR_2, HIGH);
  while (get_torque_n(2) != 0) {
    if (get_torque_n(1) < 100) {
      digitalWrite(STEP_1, HIGH);
      digitalWrite(STEP_1, LOW);
    }
    if (get_torque_n(0) < 100) {
      digitalWrite(STEP_0, HIGH);
      digitalWrite(STEP_0, LOW);
    }
    digitalWrite(STEP_2, HIGH);
    delay(200);
    digitalWrite(STEP_2, LOW);
    delay(200);
  }
  return true;
}

// Fixed: tracker0.end() -> tracker0.stop() to match AngleTracker API
int calibrate_distance_ab() {
  blind_a();
  tracker0.start();
  blind_b();
  tracker0.stop();
  return angles_to_cm(tracker0.delta());
}

int calibrate_distance_bc() {
  blind_b();
  tracker1.start();
  blind_c();
  tracker1.stop();
  return angles_to_cm(tracker1.delta());
}

int calibrate_distance_ca() {
  blind_c();
  tracker2.start();
  blind_a();
  tracker2.stop();
  return angles_to_cm(tracker2.delta());
}

uint16_t get_torque_n(int num) {
  return drivers[num]->sg_result();
}

void calibrate_angle() {
  while (get_tilt_angle() > 10.0) {
    float dir = get_tilt_dir();
    float mot_dir_diff[3];
    for (int i = 0; i < 3; i++) {
      mot_dir_diff[i] = 180*i - dir;
    }
    float max_match = find_max_v_val(mot_dir_diff);
    if (get_max_v_pos(mot_dir_diff, max_match) == 0) {
      run_b(true, 100); //tension dir.
    }
    else if (get_max_v_pos(mot_dir_diff, max_match) == 1) {
      run_c(true, 100);
    }
    else {
      run_a(true, 100);
    }
  }
}


//--------------------------------MOVEMENT----------------------------------

void move_to(int x, int y, int z) {
  int coords[3] =  {x, y, z};
  float alpha = 0;
  float beta = 0;
  float gamma = 0;
  float angles[3] = {alpha, beta, gamma};
  float path[3] = {a, b, c};
  float k = 0;
  float l = 0;
  float m = 0;
  float coeff[3] = {k, l, m};
  bool dirs[3];
  bool confirm_0 = true;
  bool confirm_1 = true;
  bool confirm_2 = true;
  float to_run[3];
  int full_turns_left[3];
  bool full_clear = false;
  bool a_clear = false;
  bool b_clear = false;
  bool c_clear = false;
  bool finished = false;
  bool a_finished = false;
  bool b_finished = false;
  bool c_finished = false;

  int counts[3];
    for (int i = 0; i < 3; i++) {
        pcnt_unit_clear_count(units[i]);  // reset all to 0
    }



  if(validate_inrange(coords)) {
    calc_delta_g_n(p0, coords, path);                 
    for (int i = 0; i < 3; i++) {                     
      if(path[i]>0) {dirs[i]=true;}                     //Dir(true/false) still unknown
      else {dirs[i]=false;}
    }
    delta_g_n_to_angle(path, angles);
    for (int i = 0; i < 3; i++) {
      to_run[i] = angles[i];
    }
    coeff_calc(path, coeff);
    tracker0.start();
    tracker1.start();
    tracker2.start();

    while(confirm_0 && confirm_1 && confirm_2) {
      run_a(dirs[0], 400*coeff[0]);
      run_b(dirs[1], 400*coeff[1]);
      run_c(dirs[2], 400*coeff[2]);
      if(read_prct0()>0) {
        confirm_0 = false;
        }
      if(read_prct1()>0) {
        confirm_1 = false;
        }
      if(read_prct2()>0) {
        confirm_2 = false;
        }
    }

    tracker0.stop();
    tracker1.stop();
    tracker2.stop();
    null_all_prcts();

    to_run[0] = to_run[0] - tracker0.delta();
    to_run[1] = to_run[1] - tracker1.delta();
    to_run[2] = to_run[2] - tracker2.delta();

    full_turns(to_run, full_turns_left);

    while(!full_clear) {
      if (full_turns_left[0] - read_prct0() > 3) {
        run_a(dirs[0], 100*coeff[0]);
      }
      else {
        a_clear = true;
      }
      if (full_turns_left[1] - read_prct1() > 3) {
        run_b(dirs[0], 100*coeff[1]);
      }
      else {
        b_clear = true;
      }
      if (full_turns_left[2] - read_prct2() > 3) {
        run_c(dirs[0], 100*coeff[2]);
      }
      else {
        c_clear = true;
      }
      if (a_clear && b_clear && c_clear) {
        full_clear = true;
      }
    }


    to_run[0] = to_run[0] - read_prct0() * 360;
    to_run[1] = to_run[1] - read_prct1() * 360;
    to_run[2] = to_run[2] - read_prct2() * 360;

    tracker0.start();
    tracker1.start();
    tracker2.start();

    while(!finished) {
      if (to_run[0]-tracker0.delta() > 10) {
        run_a(dirs[0], 400*coeff[0]);
      }
      else {
        a_finished = true;
      }
      if (to_run[1]-tracker1.delta() > 10) {
        run_b(dirs[1], 100*coeff[1]);
      }
      else {
        b_finished = true;
      }
      if (to_run[2]-tracker2.delta() > 10) {
        run_c(dirs[2], 100*coeff[2]);
      }
      else {
        c_finished = true;
      }
      if (a_finished && b_finished && c_finished) {
        finished = true;
      }
    }
  	
    calibrate_angle();
  }

}


int read_prct0() {
  int count;
  pcnt_unit_get_count(units[0], &count);
  return count;
}

int read_prct1() {
  int count;
  pcnt_unit_get_count(units[1], &count);
  return count;
}

int read_prct2() {
  int count;
  pcnt_unit_get_count(units[2], &count);
  return count;
}

void null_prct0() {
  pcnt_unit_clear_count(units[0]);
}

void null_prct1() {
  pcnt_unit_clear_count(units[1]);
}

void null_prct2() {
  pcnt_unit_clear_count(units[2]);
}

void null_all_prcts() {
  for (int i = 0; i < 3; i++) {
    pcnt_unit_clear_count(units[i]);
  }
}

void run_a(bool dir, int delay) {
  if(dir) {digitalWrite(DIR_0, HIGH);}
  else {digitalWrite(DIR_0, LOW);}
  digitalWrite(STEP_0, HIGH);
  delay(delay);
  digitalWrite(STEP_0, LOW);
  delay(delay);
}

void run_b(bool dir, int delay) {
  if(dir) {digitalWrite(DIR_1, HIGH);}
  else {digitalWrite(DIR_1, LOW);}
  digitalWrite(STEP_1, HIGH);
  delay(delay);
  digitalWrite(STEP_1, LOW);
  delay(delay);
}

void run_c(bool dir, int delay) {
  if(dir) {digitalWrite(DIR_2, HIGH);}
  else {digitalWrite(DIR_2, LOW);}
  digitalWrite(STEP_2, HIGH);
  delay(delay);
  digitalWrite(STEP_2, LOW);
  delay(delay);
}

void pcntInitRising(int gpio_num, pcnt_unit_handle_t *out_unit) {
    pcnt_unit_config_t unit_cfg = {
        .low_limit  = -32768,
        .high_limit =  32767,
    };
    pcnt_new_unit(&unit_cfg, out_unit);

    pcnt_chan_config_t chan_cfg = {
        .edge_gpio_num  = gpio_num,
        .level_gpio_num = -1,
    };
    pcnt_channel_handle_t chan;
    pcnt_new_channel(*out_unit, &chan_cfg, &chan);

    pcnt_channel_set_edge_action(chan,
        PCNT_CHANNEL_EDGE_ACTION_INCREASE,  // rising  → +1
        PCNT_CHANNEL_EDGE_ACTION_HOLD       // falling → ignore
    );

    pcnt_glitch_filter_config_t filter_cfg = { .max_glitch_ns = 1000 };
    pcnt_unit_set_glitch_filter(*out_unit, &filter_cfg);

    pcnt_unit_enable(*out_unit);
    pcnt_unit_clear_count(*out_unit);
    pcnt_unit_start(*out_unit);
}

//pcnt_unit_clear_count(units[0]);  // reset unit 0 back to 0

//--------------------------------MATH--------------------------------------


bool validate_inrange(int* pp1) {
  // TODO: make universal based on calibration data, currently hardcoded
  if (pp1[1] < (-2 * pp1[2] + 200) && pp1[1] > (0.5 * pp1[2])) {
    return true;
  }
  return false;
}


void subtract_vector(int* v1, int* v2, int* o) { // o = v2 - v1
  for (int i = 0; i < 3; i++) {
    o[i] = v2[i] - v1[i];
  }
}


float vector_length(int* vi) {
  return sqrt((float)(vi[0]*vi[0] + vi[1]*vi[1] + vi[2]*vi[2]));
}

// Fixed: internal array was int[] but function works on floats
void multiply_vector(float* v, float m, float* o) {
  for (int i = 0; i < 3; i++) {
    o[i] = v[i] * m;
  }
}

void divide_vector(float* v, float d, float* o) {
  for (int i = 0; i < 3; i++) {
    o[i] = v[i] / d;
  }
}

// Fixed: was empty
float find_max_v_val(float* v) {
  float maxVal = v[0];
  for (int i = 1; i < 3; i++) {
    if (v[i] > maxVal) maxVal = v[i];
  }
  return maxVal;
}


void calc_delta_g_n(int* pp0, int* pp1, float* o) {
  int tmp[3];

  subtract_vector(pp0, a, tmp);  float l_p0ma = vector_length(tmp);
  subtract_vector(pp0, b, tmp);  float l_p0mb = vector_length(tmp);
  subtract_vector(pp0, c, tmp);  float l_p0mc = vector_length(tmp);

  subtract_vector(pp1, a, tmp);  float l_p1ma = vector_length(tmp);
  subtract_vector(pp1, b, tmp);  float l_p1mb = vector_length(tmp);
  subtract_vector(pp1, c, tmp);  float l_p1mc = vector_length(tmp);

  o[0] = l_p1ma - l_p0ma;
  o[1] = l_p1mb - l_p0mb;
  o[2] = l_p1mc - l_p0mc;
}

// TODO: implement — convert cable length deltas to motor step angles
void delta_g_n_to_angle(float* delta_g, float* out_angles) {
  float tmp[3], tmp2[3];
  multiply_vector(delta_g, n, tmp);
  divide_vector(tmp, U, tmp2);
  multiply_vector(tmp2, 360.0, out_angles);
}

void full_turns(float* angles, int* out_turns) {
  for (int i = 0; i < 3; i++)
    out_turns[i] = (int)floor(angles[i] / 360.0f);
}

void coeff_calc(float* delta_g, float* out_coeff) {
  float coeff1[3];
  float coeff2[3];
  for(int i = 0; i < 3; i++) {
    coeff1[i] = abs(delta_g[i]);
  }
  float maxVal = find_max_v_val(coeff1);
  for (int i = 0; i < 3; i++) {
    coeff2[i] = delta_g[i] / maxVal;     // use it
  }
  for(int i = 0; i < 3; i++) {
    out_coeff[i] = 1/abs(coeff2[i]);
  }
}

float angles_to_cm(float deg) {
  float rotations = deg / 360.0f;
  float cm = rotations * PI * 8.5f;
  return cm;
}

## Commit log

2026-03-24 Fist Baseplate Design
    First Baseplate design with an ESP32-S3 for reference and one NEMA17 Motor mounted
    [0402_CA_CB_CC_CD.SLDPRT, 0402_CA_CB_CC_CD.ipt, 17HS4401S_Stepper_Motor.0001.iam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]
2026-03-25 DevSession No.3
    [baseplate.0007.ipt, baseplate.0009.ipt, baseplate.ipt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]
2026-04-02 Docs work No 1
    [0402_CA_CB_CC_CD.SLDPRT, 0402_CA_CB_CC_CD.ipt, 17HS4401S_Stepper_Motor.0002.iam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]
2026-04-02 Documantary changes of the PCBs
    [drivers.kicad_sch]
2026-04-02 Revise README with detailed project information
    Expanded project description and added key features, PCB, schematic, math, and credits sections.
2026-04-02 A little bit of this, a little bit of that ahhhh commit
    [BOM.csv, BOM.xlsx]
2026-04-02 Update PCB images in README.md
2026-04-02 Small changes again
    [17HS4401S_Stepper_Motor.step]
2026-04-02 Remove header row from BOM.csv
    Removed the header row from BOM.csv and adjusted the data accordingly.
    [BOM.csv]
2026-04-02 Correct BOM added
    [BOM.csv]
2026-04-03 Added precise and correct BOM
    [precise_adaptive_BOM.xlsx]
2026-04-24 Added .pdf fallout zine
    [backplate.0001.ipt, casing_1x1_lvl3.0002.ipt]
2026-05-03 Update README with cable routing rules
    Added cable routing guidelines for robot assembly.
2026-05-05 Update cable routing instructions in README
    Added instructions for cable mounting using zip ties.
2026-05-08 Add assembly section to README
    Added assembly instructions for the robot build process.

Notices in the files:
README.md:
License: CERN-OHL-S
